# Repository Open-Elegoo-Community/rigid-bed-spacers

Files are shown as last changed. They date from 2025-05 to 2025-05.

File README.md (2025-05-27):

# Rigid Bed Spacers
Status: Experimental

## Proposal
While working on an AWD SYNC, I observed that the Y-axis base plate IS graph is rock solid. This led me to think that the bed is a shaking mess. From experience, we know that replacing the stock springs with silicone spacers provided better stability, but there was still a lot of room for improvement. A leading hint to this was that SilencedFrosted from the Elegoo Discord mentioned he used aluminum spacers, which he filed down to the appropriate lengths after repetitive testing.

IS graph from the AWD Y-axis base plate


I propose replacing the spacers with something that anchors better to the base plate, rather than just using screws, and providing some room for adjustment. 

## Testing

Input Shaping with Silicon Spacers:


The first experiment was with aluminum spacers (bottom), a silicone washer (middle), and a fiber washer (top) so the silicone would not push through.

This tightened the IS graph, but I found the spacers I chose brought me too close to adxl345 in the center of my base plate (see AWD Y Axis). Additionally it was a pain to align the parts when remounting the bed, and the silicone was not spongy enough to keep the tension when loosening the bed screws while tramming the bed.

Fusion Model:


Input Shaping with aluminum/silicone/fiber:


I needed a way to have the spacers the height I needed without having to order them. They needed to be resistant to heat and be rigid. Why not print them? I created a quick model in Fusion and printed it in ASA. I also added a silicone washer between the spacer and the fiber washer.

Input Shaping with ASA/silicone/fiber:


## Conclusions
After several hours of printing ASA using an enclosure, I inspected the spacers. There was some small dimpling on the topmost layer. I placed a metal fender washer between the spacer and the silicone.
- The dimpling was likely due to too few top layers
- The fender washer is giving the stability needed. It will be a permanent addition to this modification.
- I would like to test with some spongier silicone

## BOM
- 4 x Fiber washer
- 1 x 0.125 inch sheet of silicone. If doubling, find a 0.25 inch thick sheet or washer.
- 4 x metal fender washers

Note: The ID of the washers needs to be 4mm.  

## Version 2 - Untested
To save on costs, I redesigned the spacer to use the original silicone spacer most of us have been using for years. 

I have not tested these yet, so I don't know if the IS performance changes. I have been busy printing other fun things, so I have not wanted to pull the bed up again and re-tram. Try it out and get back to me.

The installation is the same, except you will want the smaller hole up on top.



## How tight?
As a rule of thumb you should leave about 1mm clearance between any obstruction (like belt clips) and the insulation of the bed.

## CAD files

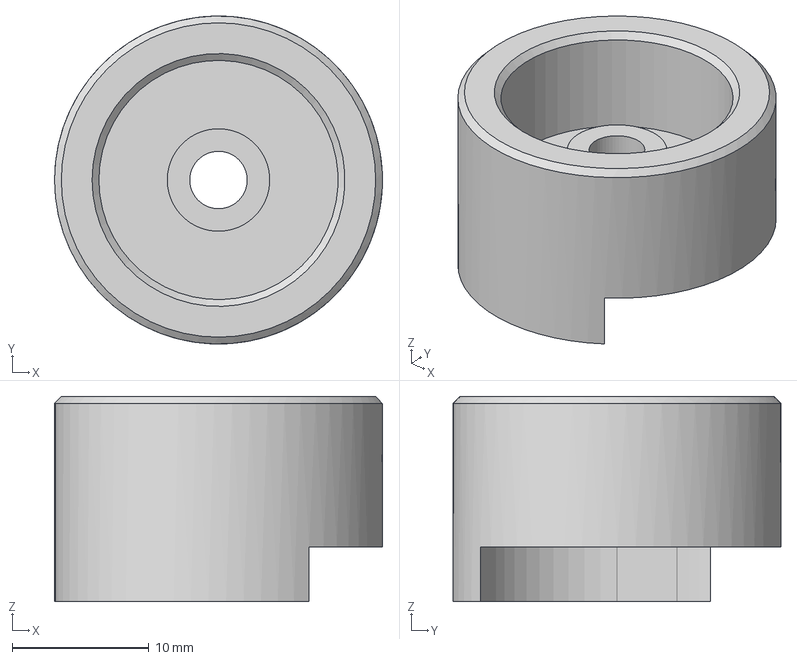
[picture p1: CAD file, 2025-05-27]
step-files/rigid-bed-spacers-v2.1.step
24.0 x 24.0 x 15.0 mm

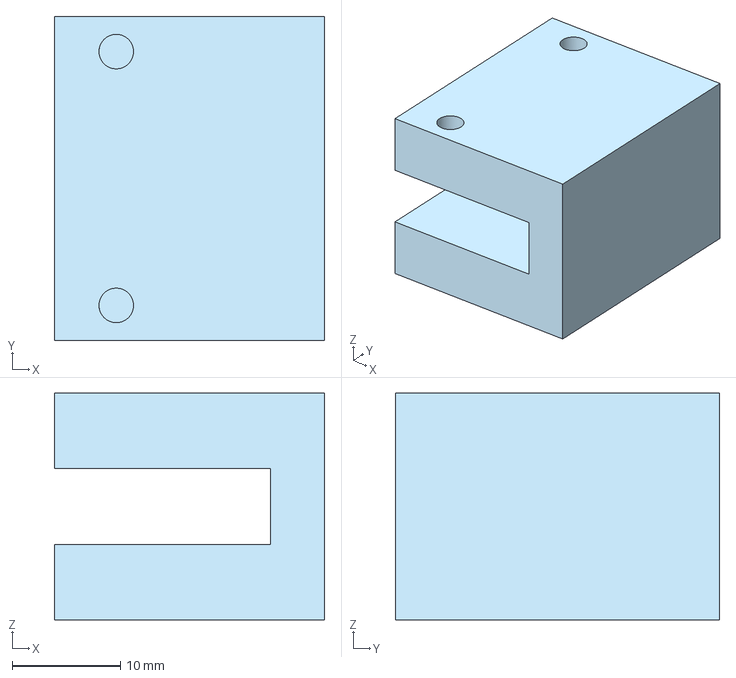
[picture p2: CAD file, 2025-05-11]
step-files/bed-mount-spacer-v1.step
25.0 x 30.0 x 21.0 mm

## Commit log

2025-05-11 Rename Bed Mount.step to bed-mount-spacer.step
    [bed-mount-spacer.step]
2025-05-11 Adding BOM
2025-05-23 Version 2. Needs the original silicone spacers.
    [rigid-bed-spacers-v2.step]
2025-05-27 Adding IS graph from the Y base plate
2025-05-27 The mounting hole is now 4.2mm instead of 4.0mm
    [rigid-bed-spacers-v2.1.step]
2025-05-27 Delete step-files/rigid-bed-spacers-v2.step
    v2.1 superceeds
    [rigid-bed-spacers-v2.step]
